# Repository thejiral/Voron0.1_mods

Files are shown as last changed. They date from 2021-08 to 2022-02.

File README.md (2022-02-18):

# Voron0.1_mods

# Modified skirts for Voron 0.1

I wanted to have skirts which fully enclose the PSU and everything else at the bottom of the V0.1, with more of a net look than the coarse honeycomb style in the original. At the same time air should still be able to circulate. 

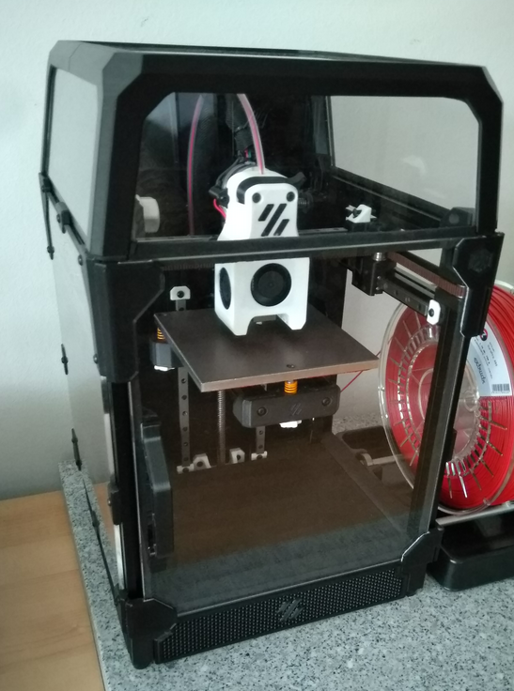
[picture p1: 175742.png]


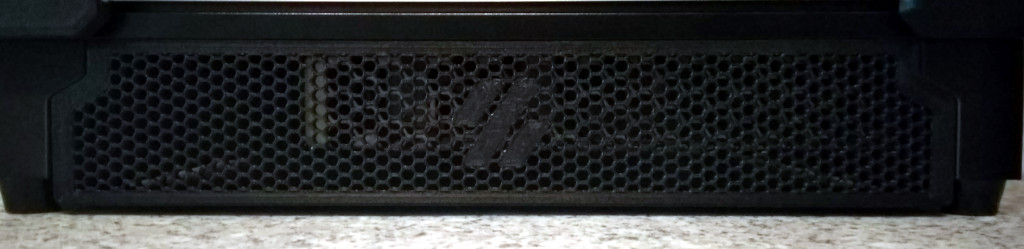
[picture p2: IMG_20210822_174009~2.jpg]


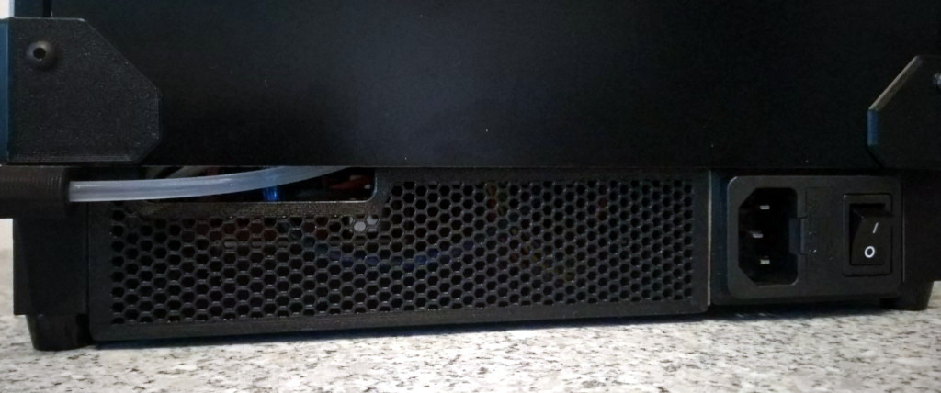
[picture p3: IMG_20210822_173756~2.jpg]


I created the honeycomb net of the skirts with Prusa slicer via infill options. The ready to print models can be be found in the 3mf file. 
Alternatively the raw component stl files are included in the zip file as well. 

The modified foot is needed for mounting panel 3. Insert 2 heat inserts (same as in the Voron 0.1 BOM). 
Panels of type 1 and 2 are mounted the same way as the original blinds but do feature throughholes for the hex key. Panel 3 is mounted with 2 M3 6mm button head screws to the rear foot right modified. At the other side I fixed Panel 3 with a bit of VHB tape at the AC Inlet. 

_Contents_

2x Panel 1 (front panel, right side panel)

1x Panel 2 (left side panel)

1x Panel 3 (back side panel)

1x Modified Rear foot

# SEPARATOR: Voron 0.1 air filter (HEPA + refillable 50 g activated carbon cassette)

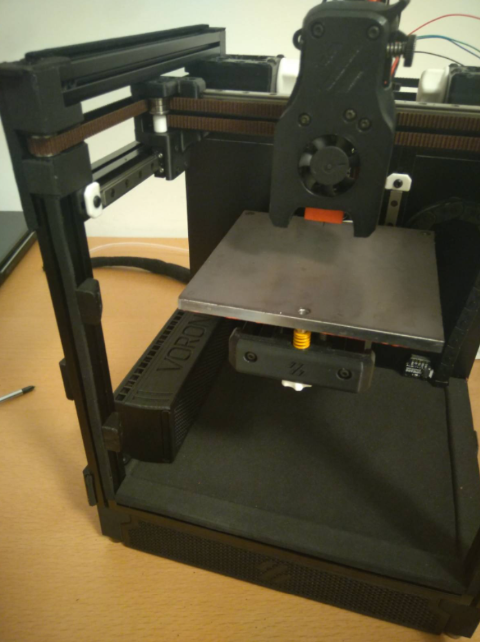
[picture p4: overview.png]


Needed components:
- 3x SEPA HY45T05A: https://www.reichelt.de/at/de/radial-luefter-45x45x5mm-5v-27db-5200u-min-gleitlager-sepa-hy45t05a-p291164.html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
- 1x HEPA filter: replacment filter for xiaomi Robot Vacuum Cleaner STYJ02YM https://www.aliexpress.com/item/4000155770683.html?spm=a2g0o.9042311.0.0.7ae94c4daSGJuo
- air purifier activated carbon pellets: https://www.luftundklima24.de/Aktivkohle-Pellets-Geruchsfilter-4-mm-1-kg-Luftfilter
  alternatively better but more expensive: Nevermore Printer Carbon: https://vonwange.com/product/nevermore-printer-carbon/
- Plastic solvent glue like UHU Plast (https://www.uhu-profishop.de/klebstoffe/kunststoffklebstoffe/137/uhu-plast-spezial-polystyrol-abs-niedrigviskos-flasche-mit-feindosierspitze-30g) or RevelL Contacta Professional (https://www.3djake.com/revell/contacta-professional)
- 2mm thick EPDM foam band 10 mm width: https://www.fugendichtband24.de/EPDM-Zellkautschuk-einseitig-selbstklebend-5m-Rolle-2mm-x-diverse-Breiten.htm
- Optionhal: 2mm thick EPDM foam mat for custom cutting: https://www.fugendichtband24.de/EPDM-Zellkautschuk-Matten-2mm-Staerke-einseitig-selbstklebend-diverse-Abmessungen.htm
- 2x M3 nut
- 2x M3 6-8 mm screws
- insulating tape
- Optional: WAGO clamps: 3x WAGO 221-613: https://www.reichelt.de/at/de/verbindungsklemme-6-mm-3-leiter-wago-221-613-p222123.html?&trstct=pol_19&nbc=1

Printed parts from ABS or ABS+ (eg. TitanX)
-SEPA-rator print files.zip (Airfilter-V3.3mf, Aifilter-V3-partb.3mf)

Assembly

2 mm EPDM foam is applied in the areas shown below. The EPDM foam should hold the fans tightly in place from both sides when housing is assembled (test tolerances before glueing). The EPDM foam should fit the fan tightly but not too tight so that the fan blade movement is obstructed. Apply one or more layer of insulating tape below the EPDM foam to fine tune the fit for the fan. 

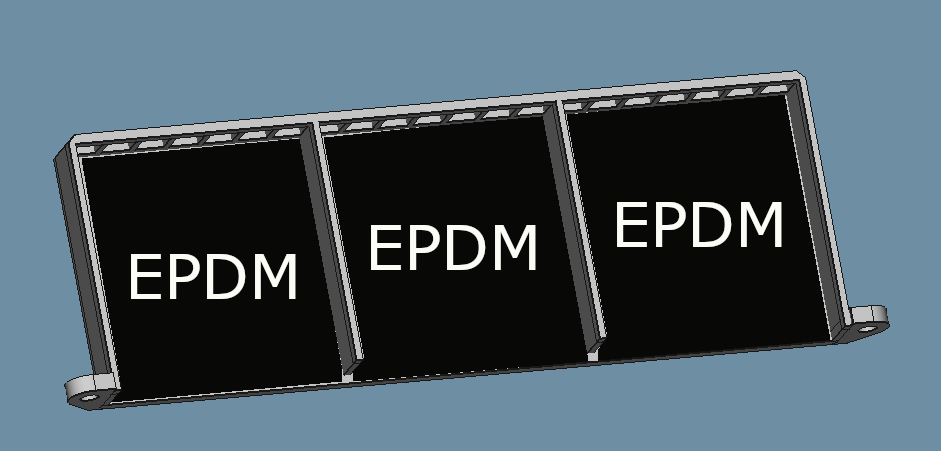
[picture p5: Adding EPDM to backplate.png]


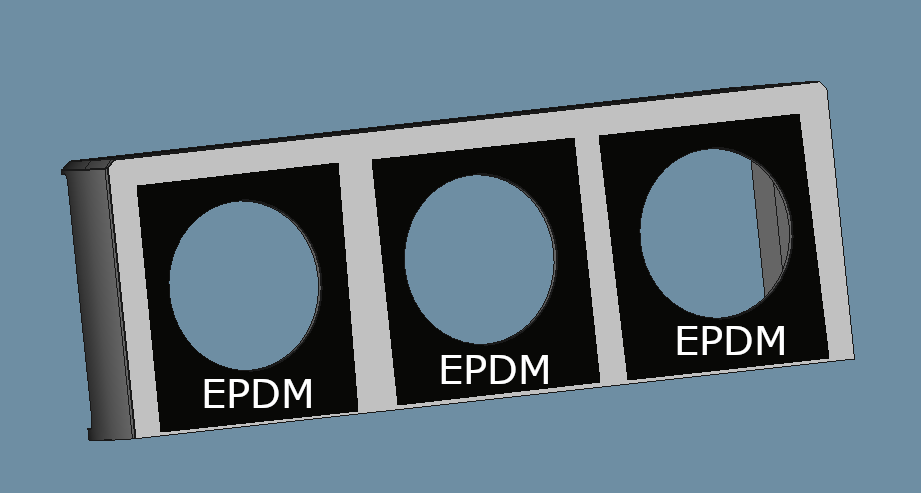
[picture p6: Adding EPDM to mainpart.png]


An EPDM band with 10 mm width (thickness: 2 mm) is applied all around the side of the top part of the active carbon cassette as can be seen in the image below:

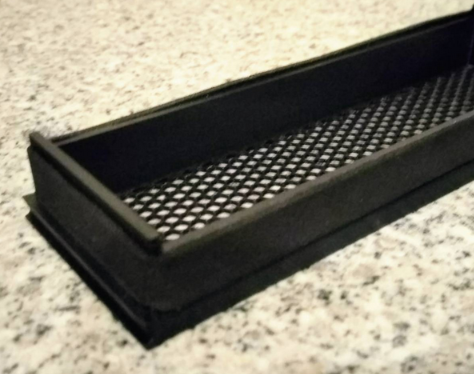
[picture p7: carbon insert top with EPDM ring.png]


In the first step of the assembly, the backplate is oriented witht the flat side down. The fans inserted with the metalic side up and the air exhaust showing to the grill of the backplate. The cables leavethe housing on the open side. 
Apply sufficient plastic glue on all the top surfaces of the backplate. The main housing is oriented with the EPDM foam towards the fans and the "Voron" label is on the same side as the grill of the backplate. The EPD free parts of the main body should be flush with the glued side of the backbplate. Make sure that both parts are aligned well and seamlessly with each other and compress the EPDM foam with sufficient pressure. Put books or other heavy weights (1-2kg) to maintain that pressure and gapless contact of thet wo surfaces for at least 24h. 

The assembled body can be mounted with the two screw holes to 2 nuts inserted into the bottom frame. Alternatively it can be mounted with VHB-tabe to the frame.

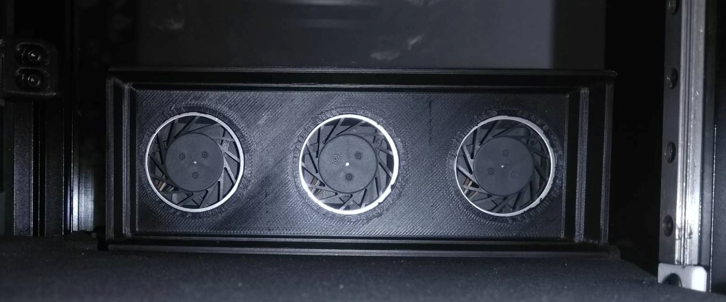
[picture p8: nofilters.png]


By drilling a small hole just below airfilter, the cables can exit the chamber and be connected via WAGO clamps to continuing cables.The yellow cables are not needed and can be cut and isolated. Red (minus) and black (plus) are connected to the 5V converter of the VO.1 and the orange cable is transmitting the PWM signal and is connected to a hardware PWM pin on the Raspberry Pi (eg GPIO12 on a Raspberry Pi 3). (https://pinout.xyz/pinout/pwm#)

The HEPA filter is removed from the clear plastic cassette it is sold in and is inserted into the airfilter body with the lash looking outwards. 

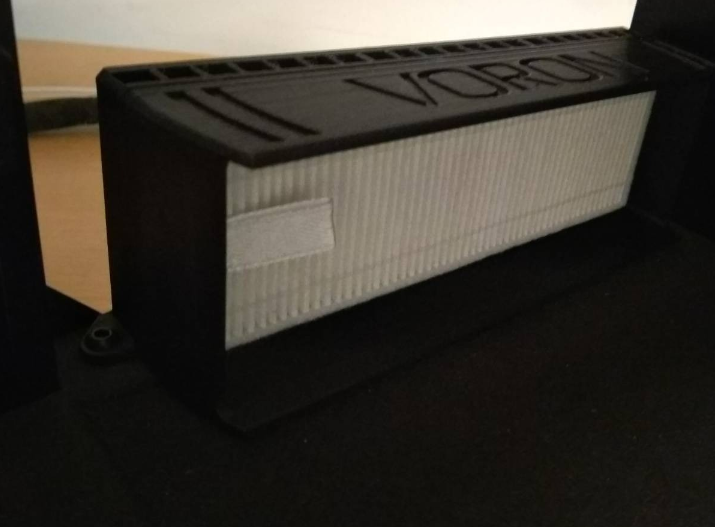
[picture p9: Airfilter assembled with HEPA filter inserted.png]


The bottom of the cassette is filled flush with active carbon pellets and combined with the top part

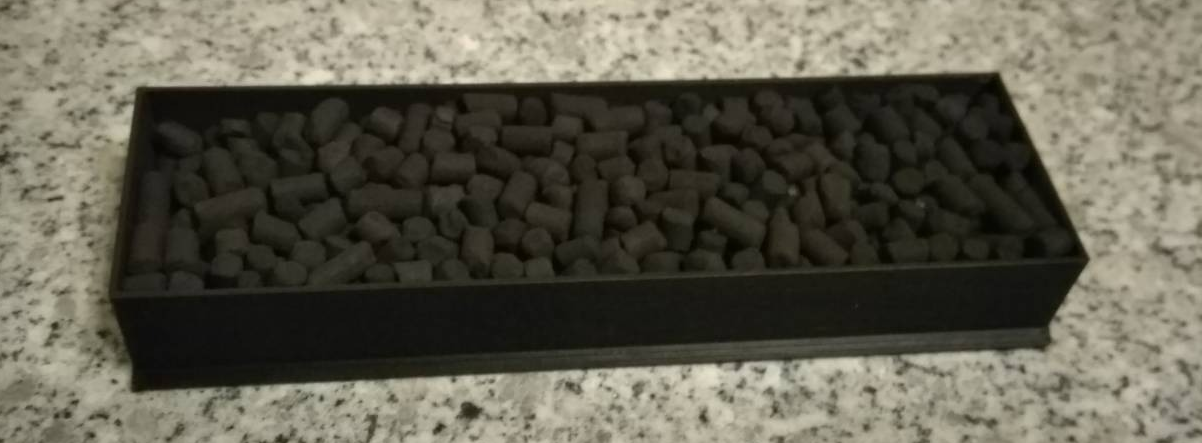
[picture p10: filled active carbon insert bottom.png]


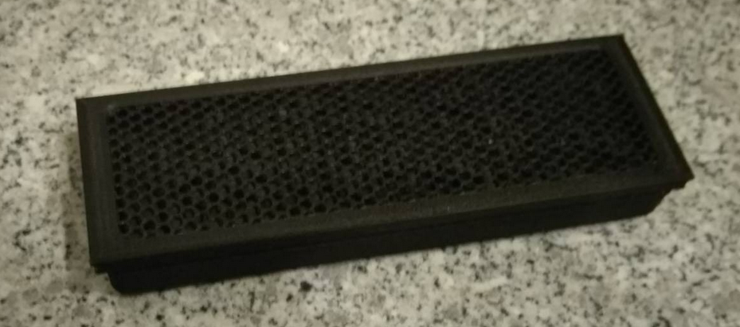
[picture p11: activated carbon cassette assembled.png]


The cassette is inserted into the airfilter body and the filter is ready for operation. If no PWM signal is provided the fans will run at full speed. If the PWM cables are connected to a Hardware PWM Pin of the Raspberry Pi it can be controlled among others with the Octoprint plugin "HardwarePWM" (set frequency to 23kHz). 
 
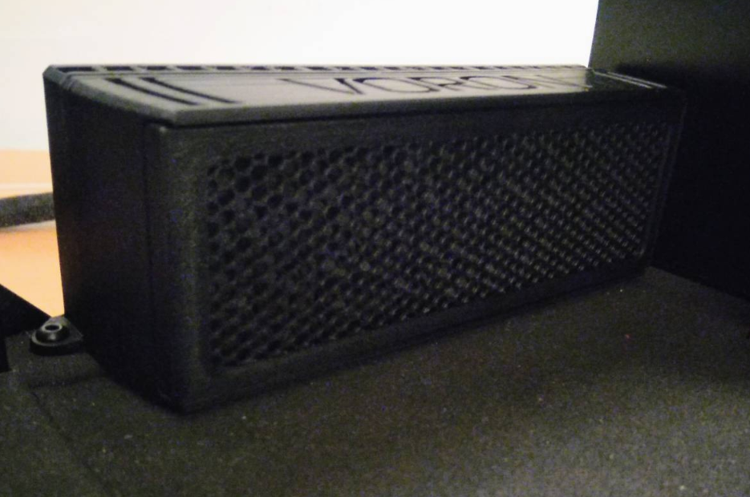
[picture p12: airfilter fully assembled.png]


Activated carbon should be exchanged frequently, the HEPA filter has a longer life cycle and needs to be replaced when airflow decreases.

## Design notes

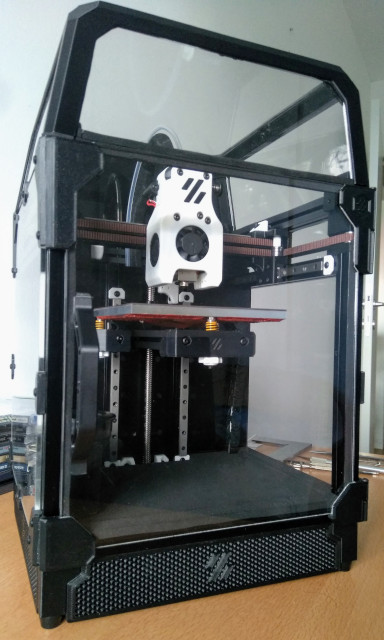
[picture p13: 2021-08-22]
IMG_20210821_091123~2.jpg

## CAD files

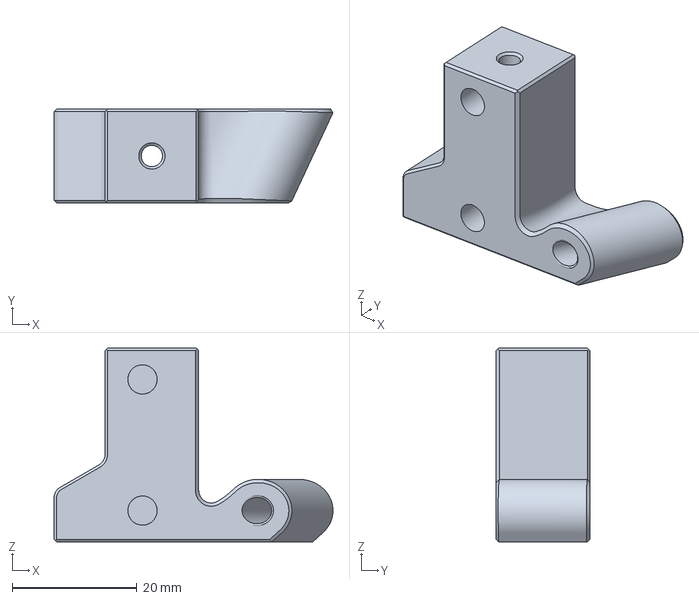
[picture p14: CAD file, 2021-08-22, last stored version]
Foot rear right modified.3mf
44.7 x 15.0 x 31.0 mm

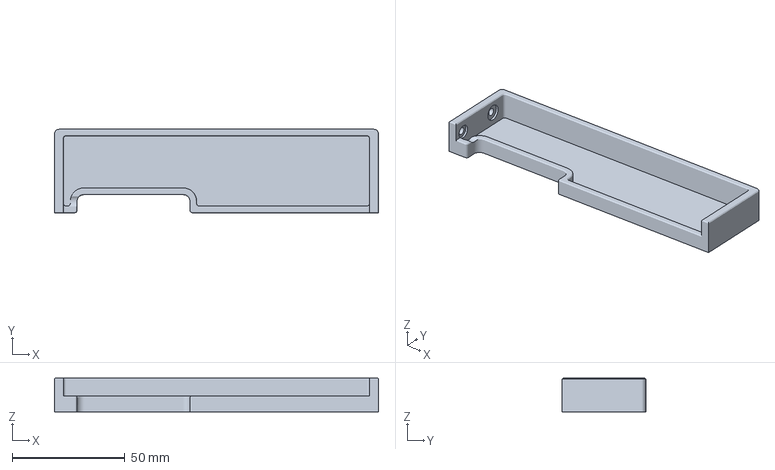
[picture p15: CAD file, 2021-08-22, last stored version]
Panel3.3mf
143.5 x 37.0 x 15.0 mm

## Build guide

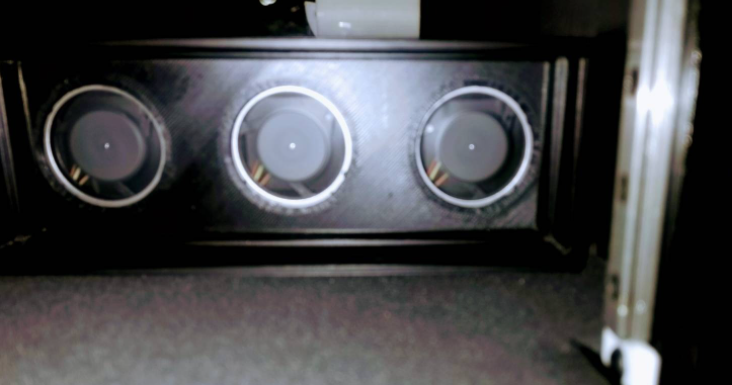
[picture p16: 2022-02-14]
Assembled airfilter without HEPA filter and AC cassette.png
